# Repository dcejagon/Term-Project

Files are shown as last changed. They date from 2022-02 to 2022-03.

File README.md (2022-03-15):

# Term Project Report 
### Description 
For our term project, have designed a 2.5 axis plotter. This plotter will have 
a rotating arm with a carriage that extends out on the arm. The plotter will move
in both the R and Theta directions to achieve the plotting of an image. 
arm, with the actual pen extending out on the arm. The base of the plotter will 
hold 2 motors; the first motor will control the rotation of the arm similar to 
the motion of  a windshield wiper (Theta), while the second motor will change the radial 
position of the pen carrier(R). The radial motor will control the pen location by 
moving the sharpie carriage using belts driven by pulleys. The pen carriage will have a servo motor 
that controls the up and down motion of the pen (0.5 Axis). This plotter will 
convert an image to X-Y Gcode, and then we will convert that into cylindrical, 
R-Theta, coordinates due to our system being inherently non-rectilinear. 
In addition, This plotter should be relatively low cost ~$15 per person. 
We intend to use materials commonly used in 3D printing like Aluminum T-Slot 
extrusion and V-Slot bearings. The full bill of materials and cost breakdown 
is seen below. Items that have a "-" in the cost column are parts that we have 
access to with no cost. Our main source for parts will be Amazon to eliminate 
shipping costs. Team members have access to 3D printers, which will be used 
to fabricate custom parts such as mounting brackets, main Sharpie carriage, 
and motor mounts at no additional cost.  
### Use
This 2.5 axis plotter is intended to be used to plot images on a piece of paper. 
However, the main carriage of this plotter could be easily changed to accommodate 
a CO2 laser or small cutting blade to turn the plotter into a laser cutter or a 
vinyl cutter.  This project was just intended to be used by our team to demonstrate
many of the concepts that we learned in ME 405, Mechatronics, however I think it would 
be interesting to redesign some of the motor mounts to accept more consumer grade motors
so that we could each produce our own plotter for personal use. 
### BOM and Estimated Cost
| Qty. | Part | Source | Est. Cost |
|:----:|:---|:---|:---:|
|  2 | Pittperson Gearmotors | ME405 Tub | - |
|  1 | Nucleo with Shoe | ME405 Tub | - |
|  1 | Motor H-Bridge | ME405 Tub | - |
|  1 | Purple Sharpie&trade; | Personal Supply | - |
|  1 | Servo Motor | Personal Supply | - |
|  1 | Limit Switch pack | Amazon | $6.99 |
|  1 | Vbearings and Belt | Amazon | $18.59  |
|  1 | 2020 Al Extrusion | Amazon | $19.99  |

### Sketch of Pen Plotter 
The initial sketch of our system is shown below. This design features preliminary
dimensions and a sketch of the general shape and motion of our system. The blue lines
depict the direction that the system may move, and the axis that this motion occurs on.
For example, the curved blue arrows and the Theta axis show that our "arm" will rotate
about the larger base (Radius of 1"). The main features of this sketch are the base,
arm, carriage, and wheel. The exact shape and location of these parts, along with 
parts that are less significant to the general motion of our system are shown in the 
full system CAD model below. One thing that is not depicted in this sketch is how 
we actuated the 0.5 axis that will move the Sharpie up and down. This will be shown
in detail in the Main Carriage Subsystem CAD model section below. 

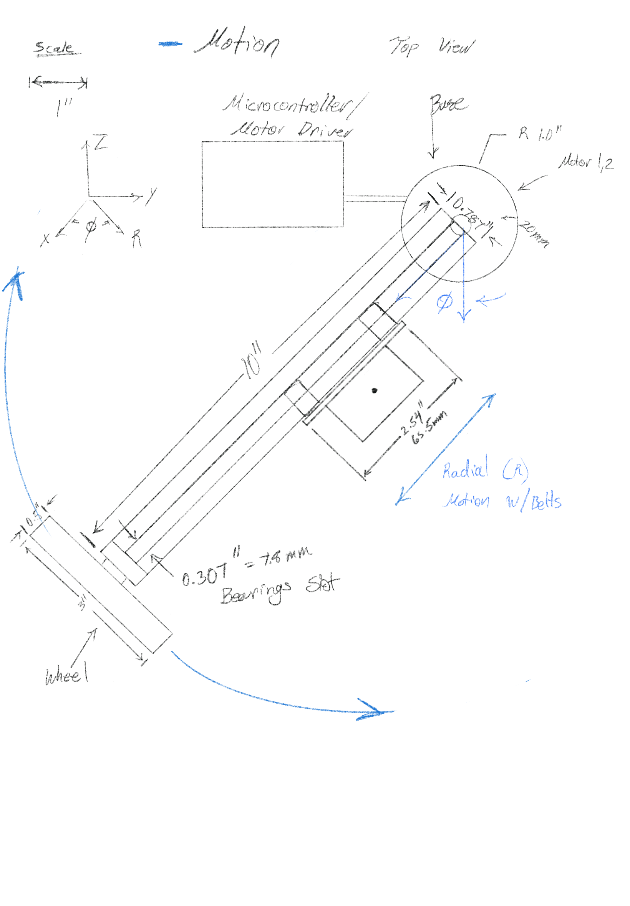
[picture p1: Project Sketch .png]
Drawing of Proposed Plotter

Initial Sketch of Plotter 

### Full System CAD Model
The image below shows our full system CAD model. The parts that are a light orange 
color are some the parts that we 3D printed. This image shows how the system will move;
the motor that is attached to the aluminum extrusion will rotate a pulley. This pulley 
will rotate a belt, who's ends are attached to the sharpie carriage in the slots. The
belt will be tensioned by being attached to a idle pulley on the aluminum extrusion
near the wheel.

The theta direction will also be actuated with belts and pulleys. The Theta motor
is fixed with set screws into the large, orange, triangle shaped, bracket. This motor 
has a pulley on it that is in plane with the larger red pulley in the image. These pulleys
have a belt that is attached around them, so when the motor rotates, the large 
pulley is rotated. This large red pulley is fixed to the aluminum extrusion with 
two bolts. This means that the red pulley cannot rotate relative to the extrusion,
which allows us to rotate the extrusion by rotating the Theta motor. This pulley is 
extended to hold three ball bearings that are press fit into the pulley. 
These bearings rotate on a 3/8" bolt which is the "axle" for our arm to rotate on.
In addition, the red pulley is around twice the diameter of the pulley attached to the motor 
which gives us a larger gear ratio to transmit more torque from the motor to our system. 

The large wheel on the end of the extrusion is necessary to provide support to the 
end of our arm. The wheel prevents the arm from being a cantilevered beam, and reduces
the torque required to rotate the arm. 

Each of the motor mounting brackets have holes that have heat set inserts in them
so we can use screws to act as set screws to hold the motors in place. 

The motor bracket on the aluminum extrusion also holds a limit switch. This switch 
will act as a "kill switch" so that if the motor ever hits it, the motor duty will 
instantly be set to zero. This switch was initially going to be used to home the R
axis, however we had an issue where our motors would free-spin after the program finished
running, and changing the switch to be a kill switch prevents the mechanical system 
from tearing itself apart and the motors from burning up. 

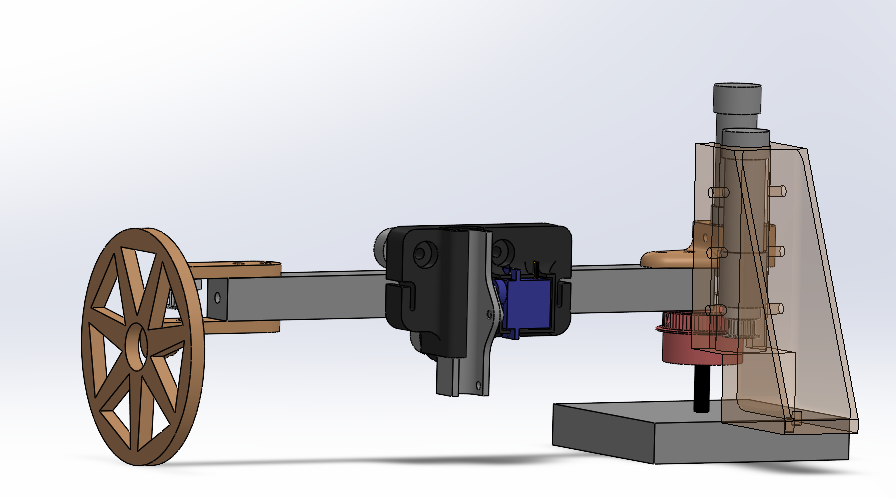
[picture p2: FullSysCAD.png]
CAD of Full System, Front

CAD model of full system front view

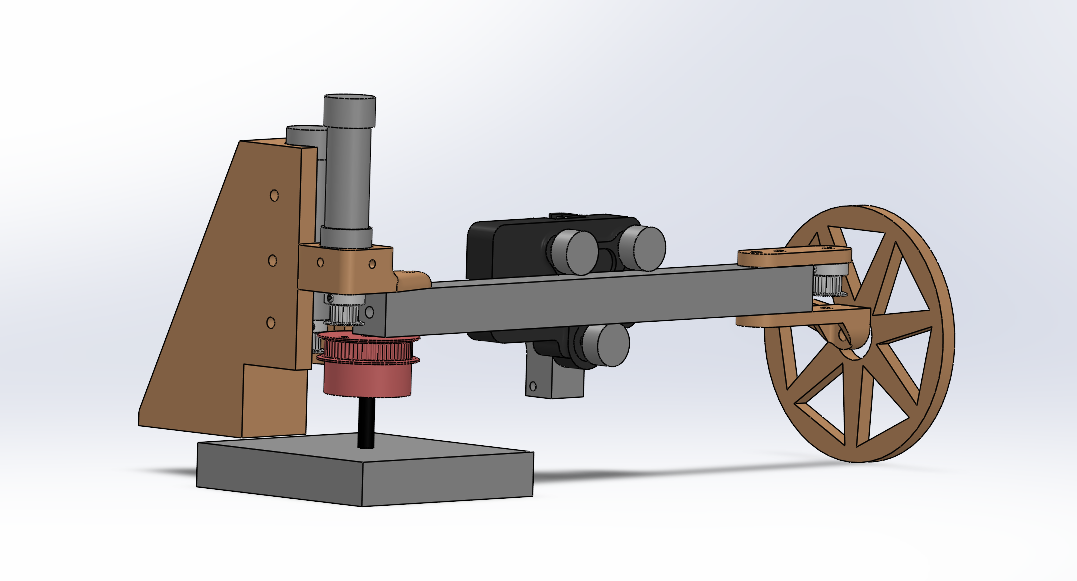
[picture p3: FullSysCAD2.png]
CAD of Full System, Rear

CAD model of full system rear view

### Main Carriage Subsystem CAD Model

The image below shows the main sharpie carriage in more detail. The black piece
is the "carriage" that has bolts that go through it and have V-Slot bearings on
the back side (shown as the gray cylinders at the top of the image). These bearings
ride in the T-slot on the aluminum extrusion, allowing for smooth, linear movement
of the carriage on the extrusion. 

The blue rectangular piece is the servo motor that is responsible for actuating our 
half axis. The servo motor is attached to the carriage with rubber bands so it can
be repurposed for other projects. The servo motor has a small link (white part) attached to it.
This link has a hole on one side to press fit onto the servo shaft, and a slot 
on the other. This slot will have a "pin" that attaches to the sliding carriage 
where the Sharpie is attached. When the servo motor is rotated, the slotted linkage
rotates , which pushes against pin attached to the Sharpie carriage, causing 
vertical movement of the Sharpie carriage. 

The small, "r" shaped slots on either side of the main carriage are where the ends
of the belt to move the main carriage are attached.  

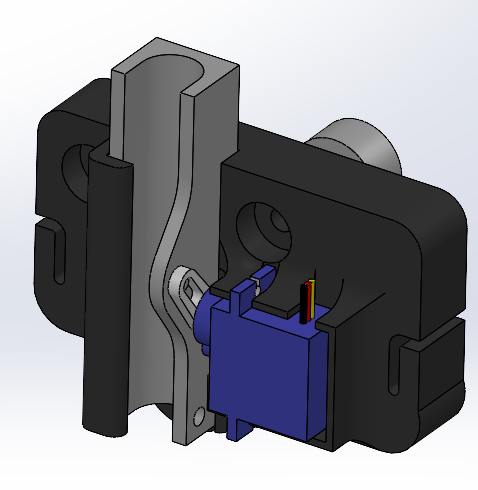
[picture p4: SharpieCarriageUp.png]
CAD of main carriage, raised

CAD model of main carriage in "up" position

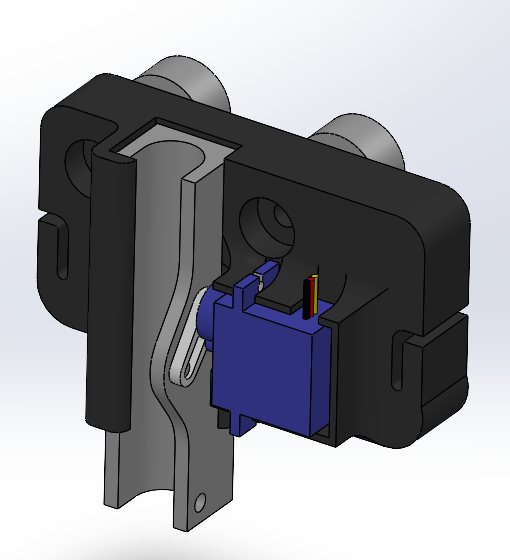
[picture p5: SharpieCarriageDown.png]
CAD of main carriage, lowered

CAD model of main carriage in "down" position

### Software Design Overview
In order to generate the path that the pen should take, we used http://jscut.org/jscut.html# ,
a website that accepts SVG images and converts it to GCODE. This website was nice, because 
each of the GCODE lines were G1, which is the call for a straight line. The GCODE that 
this website outputs is a series of straight lines that are very short (around 0.001"). 
This means, we essentially have a list of X-Y coordinates that trace out our image. 

We then use the file GcodeInterpreter.py, to take each line of GCODE, pull out the 
desired X-Y coordinates, and then preform some math to convert these to R-Theta
coordinates. From these R-Theta coordinates, we use our known gear ratios to write
the desired R Motor angle and Theta Motor angle to their own .txt files. 

We then read each line of these files one at a time, to generate the desired
R and Theta motor setpoints. 

We then input these setpoints into a closed loop controller which will calculate the
required duty to move the motor so that the motor position reaches the setpoint. 

We determine the motor position from encoders that are attached to the motor shaft. 

The timing of these different tasks was something that we had some trouble implementing,
however, we were able to achieve the proper timing by adding two buffer variables. 
Essentially, first, we get both setpoints, then, the motors rotate to try and reach that setpoint
next, we check to see if each motor has reached its setpoint (or within a few degrees of it).
If the motor has not reached this setpoint, we do not get another setpoint. As soon as the motor 
reaches its setpoint, on its next loop around the task diagram, we generate a new setpoint. 
This process allows us to be sure that our motors reach their desired setpoint before they
transition to another one. 

In addition, the motor control task has three sub-tasks running. 
First, we read the motor position from the encoders. Next, we run the closed loop
controller. Last, we use the motor duty that comes out of the closed loop file
to run our motors at this duty. It is important that the motor control task runs 
as quickly as possible so that the closed loop controller can calculate be sure the
motor reaches the desired position as quickly as possible, while minimizing overshoot. 

Lastly, we had a task that controlled the limit switch reading and servo motor actuation.
The limit switch subtask checks the limit switch value (0 or 1) and decides if the duty needs to be set 
to zero. The servo motor subtask checks to see if the pen should lifted or lowered,
and then raised or lowers the servo motor. 

A more in-depth description of each file, along with the overall software structure
can be found in the links below. 

Full Source Code:          [https://github.com/dcejagon/Term-Project/blob/e9a6a358911b557f958eb8ccfb334c0a805cc6d8/src]

Documentation:             [https://dcejagon.github.io/Term-Project/index.html]

### System Performance and Results
We tested our system by trying to draw several images. We attempted to draw a 
Cal Poly logo, as well as a simple rectangle. These test revealed some errors
in our software design somewhere. We were able to successfully draw, however, we
were not able to produce a discernable image. We believe that it has something to 
do with the path the pen is taking between the points. For the rectangle, we can see
the image has four distinct "points", but the paths between these points is anything 
but a straight line. With more time, we would be able to hammer out the bugs in
our system and correct the paths between points. Overall, we are happy with what 
we were able to accomplish during the entirety of this project. 

### Possible System Modifications
Outside of the path issue mentioned above, one of our biggest issues was the 
resolution our motors were able to accomplish. We think that we prioritized speed 
more than accuracy, which means we tried to minimize the gear ratios that we were 
using. The motors we were using have a minimum duty that will make them rotate. 
Significant issues arise when the desired position is too close to the previous 
position, because the motor cannot rotate with this small of a duty. By increasing 
the gear ratios we are using significantly, we would increase the resolution that 
we can plot. Instead of 2 points that are very close producing a duty of 10 for example,
with the increased gear ratio, we can have the same two points, produce a duty of 50 or even 100.
This would allow for our plotted pictures to be very clear, with the effect of 
significantly decreasing the speed at which we can plot. 

In addition, we should have had our platform 
that the parts are mounted to extend out so that every part of the system rests
on this platform. This would minimize the amount of flex from the point of rotation
to the end of the extrusion. 

One of the last things that was somewhat of an issue, was our heat set inserts. 
When we tightened the screws to hold the motor in place, the inserts began to pull 
out of their holes. We think this could be resolved by reducing the size of the holes
or using different inserts. 

Some of the things that do not need modification is how the main carriage rides on
the aluminum extrusion. We are able to produce a very smooth linear movement of the
carriage when we rotate the motor. In addition, the way the way our different tasks
interacted with each other was largely successful. Once we figured out the proper 
timing, our software worked as intended, and ironing out the path issue would
not require much rework to our task layout. 

Here is the link to the folder that contains all of our Solidworks files as well
as STL's used for 3D printing. 
[https://github.com/dcejagon/Term-Project/tree/bce21b94aa009a9af5754362cd7ddc3f18eb79eb/TP%20CAD]

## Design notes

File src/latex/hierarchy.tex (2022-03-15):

\doxysection{Class Hierarchy}
This inheritance list is sorted roughly, but not completely, alphabetically\+:\begin{DoxyCompactList}
\item \contentsline{section}{task\+\_\+share.\+Base\+Share}{\pageref{classtask__share_1_1BaseShare}}{}
\begin{DoxyCompactList}
\item \contentsline{section}{task\+\_\+share.\+Queue}{\pageref{classtask__share_1_1Queue}}{}
\item \contentsline{section}{task\+\_\+share.\+Share}{\pageref{classtask__share_1_1Share}}{}
\end{DoxyCompactList}
\item \contentsline{section}{Encoder\+Driver.\+Encoder\+Driver}{\pageref{classEncoderDriver_1_1EncoderDriver}}{}
\item \contentsline{section}{REncoder.\+Encoder\+Driver}{\pageref{classREncoder_1_1EncoderDriver}}{}
\item \contentsline{section}{Gcode\+Interpreter.\+Gcode\+Interpreter}{\pageref{classGcodeInterpreter_1_1GcodeInterpreter}}{}
\item \contentsline{section}{Servo\+Motor\+F.\+Limit\+Switch}{\pageref{classServoMotorF_1_1LimitSwitch}}{}
\item \contentsline{section}{Motor\+Driver.\+Motor\+Driver}{\pageref{classMotorDriver_1_1MotorDriver}}{}
\item \contentsline{section}{shares.\+Queue}{\pageref{classshares_1_1Queue}}{}
\item \contentsline{section}{RMotor\+Control.\+RClosed\+Loop}{\pageref{classRMotorControl_1_1RClosedLoop}}{}
\item \contentsline{section}{Servo\+Motor\+F.\+Servo\+MotorF}{\pageref{classServoMotorF_1_1ServoMotorF}}{}
\item \contentsline{section}{shares.\+Share}{\pageref{classshares_1_1Share}}{}
\item \contentsline{section}{cotask.\+Task}{\pageref{classcotask_1_1Task}}{}
\item \contentsline{section}{cotask.\+Task\+List}{\pageref{classcotask_1_1TaskList}}{}
\item \contentsline{section}{Theta\+Motor\+Control.\+Theta\+Closed\+Loop}{\pageref{classThetaMotorControl_1_1ThetaClosedLoop}}{}
\end{DoxyCompactList}

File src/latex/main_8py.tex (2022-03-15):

\hypertarget{main_8py}{}\doxysection{main.\+py File Reference}
\label{main_8py}\index{main.py@{main.py}}

File to control the main function of our hardware.  

\doxysubsection*{Functions}
\begin{DoxyCompactItemize}
\item 
\mbox{\Hypertarget{main_8py_a4b8585ab93623990a26b69bcdc14b238}\label{main_8py_a4b8585ab93623990a26b69bcdc14b238}} 
def {\bfseries main.\+task1\+\_\+fun} ()
\begin{DoxyCompactList}\small\item\em ! runs tasks and functions for the first motor \end{DoxyCompactList}\item 
\mbox{\Hypertarget{main_8py_a6a1e59f7b9547c8b4149f09992218273}\label{main_8py_a6a1e59f7b9547c8b4149f09992218273}} 
def {\bfseries main.\+task2\+\_\+fun} ()
\item 
\mbox{\Hypertarget{main_8py_acc62ac11d1a297e1641a94216ce982c7}\label{main_8py_acc62ac11d1a297e1641a94216ce982c7}} 
def {\bfseries main.\+task3\+\_\+fun} ()
\end{DoxyCompactItemize}
\doxysubsection*{Variables}
\begin{DoxyCompactItemize}
\item 
\mbox{\hyperlink{main_8py_a87970a5d04059649a6735a2a405477ea}{main.\+en\+\_\+pin}} = pyb.\+Pin (pyb.\+Pin.\+board.\+PA10, pyb.\+Pin.\+OUT\+\_\+\+PP)
\begin{DoxyCompactList}\small\item\em This variable is for the enable pin for motor 1. \end{DoxyCompactList}\item 
\mbox{\hyperlink{main_8py_aad671708cd06aec861a24b45c56c74aa}{main.\+in1pin}} = pyb.\+Pin (pyb.\+Pin.\+board.\+PB4, pyb.\+Pin.\+OUT\+\_\+\+PP)
\begin{DoxyCompactList}\small\item\em This variable is for the first pin of motor 1. \end{DoxyCompactList}\item 
\mbox{\hyperlink{main_8py_ae821c4ba5f2d29414e6008d3caaf5109}{main.\+in2pin}} = pyb.\+Pin (pyb.\+Pin.\+board.\+PB5, pyb.\+Pin.\+OUT\+\_\+\+PP)
\begin{DoxyCompactList}\small\item\em This variable is for the second pin of motor 1. \end{DoxyCompactList}\item 
\mbox{\Hypertarget{main_8py_a4fe20a9d36fdc5b4ea50d88f43f6ed54}\label{main_8py_a4fe20a9d36fdc5b4ea50d88f43f6ed54}} 
int {\bfseries main.\+timer} = 3
\begin{DoxyCompactList}\small\item\em This variable is for the timer number associated with motor 1. \end{DoxyCompactList}\item 
\mbox{\hyperlink{main_8py_aa7d20efaf3b8775924472f1e6ee9abe1}{main.\+en\+\_\+pin2}} = pyb.\+Pin (pyb.\+Pin.\+board.\+PC1, pyb.\+Pin.\+OUT\+\_\+\+PP)
\begin{DoxyCompactList}\small\item\em This variable is for the enable pin for motor 2. \end{DoxyCompactList}\item 
\mbox{\hyperlink{main_8py_af69bac68438b6a4b323fd2da4fb0ab10}{main.\+in1pin2}} = pyb.\+Pin (pyb.\+Pin.\+board.\+PA0, pyb.\+Pin.\+OUT\+\_\+\+PP)
\begin{DoxyCompactList}\small\item\em This variable is for the first pin of motor 2. \end{DoxyCompactList}\item 
\mbox{\hyperlink{main_8py_ae006dd22d15c7224f4271cdd30be3c3e}{main.\+in2pin2}} = pyb.\+Pin (pyb.\+Pin.\+board.\+PA1, pyb.\+Pin.\+OUT\+\_\+\+PP)
\begin{DoxyCompactList}\small\item\em This variable is for the second pin of motor 2. \end{DoxyCompactList}\item 
\mbox{\Hypertarget{main_8py_ab6598c969df592e6fefba95d3ae53da0}\label{main_8py_ab6598c969df592e6fefba95d3ae53da0}} 
int {\bfseries main.\+timer2} = 5
\begin{DoxyCompactList}\small\item\em This variable is for the timer number associated with motor 2. \end{DoxyCompactList}\item 
\mbox{\hyperlink{main_8py_a9302e8220a79b02f30da6df3b3b72db9}{main.\+ENCpin1}} = pyb.\+Pin (pyb.\+Pin.\+board.\+PB6)
\begin{DoxyCompactList}\small\item\em This variable is for the frist encoder pin of encoder 1. \end{DoxyCompactList}\item 
\mbox{\hyperlink{main_8py_a335a37a6d6e27c40302538c0b03bea08}{main.\+ENCpin2}} = pyb.\+Pin (pyb.\+Pin.\+board.\+PB7)
\begin{DoxyCompactList}\small\item\em This variable is for the second encoder pin of encoder 1. \end{DoxyCompactList}\item 
\mbox{\Hypertarget{main_8py_aee15e1a13ec15c40e22322b1ca997d5a}\label{main_8py_aee15e1a13ec15c40e22322b1ca997d5a}} 
int {\bfseries main.\+timernumber} = 4
\begin{DoxyCompactList}\small\item\em This variable is for the timer number associated with encoder 1. \end{DoxyCompactList}\item 
\mbox{\hyperlink{main_8py_a630b3ace839f6b7b34761f44d2161d6e}{main.\+ENC2pin1}} = pyb.\+Pin (pyb.\+Pin.\+board.\+PC6)
\begin{DoxyCompactList}\small\item\em This variable is for the frist encoder pin of encoder 2. \end{DoxyCompactList}\item 
\mbox{\hyperlink{main_8py_a4c4b6becca7ef9e44742e3eecca211a9}{main.\+ENC2pin2}} = pyb.\+Pin (pyb.\+Pin.\+board.\+PC7)
\begin{DoxyCompactList}\small\item\em This variable is for the second encoder pin of encoder 2. \end{DoxyCompactList}\item 
\mbox{\Hypertarget{main_8py_ac52fc1272d4326318676d53ec92ad746}\label{main_8py_ac52fc1272d4326318676d53ec92ad746}} 
int {\bfseries main.\+timernumber2} = 8
\begin{DoxyCompactList}\small\item\em This variable is for the timer number associated with encoder 2. \end{DoxyCompactList}\item 
\mbox{\hyperlink{main_8py_a4f911a1828df7baf0a3e060305223057}{main.\+duty1}} = \mbox{\hyperlink{classtask__share_1_1Share}{task\+\_\+share.\+Share}} (\textquotesingle{}f\textquotesingle{}, thread\+\_\+protect = False, name = \char`\"{}Duty\+\_\+1\char`\"{})
\begin{DoxyCompactList}\small\item\em Shared Variable for duty of motor 1. \end{DoxyCompactList}\item 
\mbox{\hyperlink{main_8py_ac52b4d68543efdb75c86ea26b8171085}{main.\+duty2}} = \mbox{\hyperlink{classtask__share_1_1Share}{task\+\_\+share.\+Share}} (\textquotesingle{}f\textquotesingle{}, thread\+\_\+protect = False, name = \char`\"{}Duty\+\_\+2\char`\"{})
\begin{DoxyCompactList}\small\item\em Shared Variable for duty of motor 2. \end{DoxyCompactList}\item 
\mbox{\hyperlink{main_8py_a35d82fc6f6309ca098efc4fb6ab555ff}{main.\+Enc\+Position}} = \mbox{\hyperlink{classtask__share_1_1Share}{task\+\_\+share.\+Share}} (\textquotesingle{}h\textquotesingle{}, thread\+\_\+protect = False, name = \char`\"{}Position\+\_\+1\char`\"{})
\begin{DoxyCompactList}\small\item\em Shared Variable position of encoder 1. \end{DoxyCompactList}\item 
\mbox{\hyperlink{main_8py_a9ba3c81db34dbcdf4b55584e0f0fb2e2}{main.\+Enc\+Position2}} = \mbox{\hyperlink{classtask__share_1_1Share}{task\+\_\+share.\+Share}} (\textquotesingle{}h\textquotesingle{}, thread\+\_\+protect = False, name = \char`\"{}Position\+\_\+2\char`\"{})
\begin{DoxyCompactList}\small\item\em Shared Variable position of encoder 2. \end{DoxyCompactList}\item 
\mbox{\hyperlink{main_8py_a1a9d6b768cfb91f02bd7d18cdc9fbd20}{main.\+Kp1}} = \mbox{\hyperlink{classtask__share_1_1Share}{task\+\_\+share.\+Share}} (\textquotesingle{}f\textquotesingle{}, thread\+\_\+protect = False, name = \char`\"{}Proportional\+\_\+\+Gain1\char`\"{})
\begin{DoxyCompactList}\small\item\em Shared variable for proportional gain of motor 1. \end{DoxyCompactList}\item 
\mbox{\hyperlink{main_8py_ab96cfd6fecea16d8801129f649f7b971}{main.\+Kp2}} = \mbox{\hyperlink{classtask__share_1_1Share}{task\+\_\+share.\+Share}} (\textquotesingle{}f\textquotesingle{}, thread\+\_\+protect = False, name = \char`\"{}Proportional\+\_\+\+Gain2\char`\"{})
\begin{DoxyCompactList}\small\item\em Shared variable for proportional gain of motor 2. \end{DoxyCompactList}\item 
\mbox{\hyperlink{main_8py_a7b85b2b65758a558f3e3032f3950c355}{main.\+setpoint1}} = \mbox{\hyperlink{classtask__share_1_1Share}{task\+\_\+share.\+Share}} (\textquotesingle{}f\textquotesingle{}, thread\+\_\+protect = False, name = \char`\"{}Set\+\_\+\+Point1\char`\"{})
\begin{DoxyCompactList}\small\item\em Shared variable for the setpoint of motor 1. \end{DoxyCompactList}\item 
\mbox{\hyperlink{main_8py_aaa37d4ce2366d78815bdf5dd79d8cc08}{main.\+setpoint2}} = \mbox{\hyperlink{classtask__share_1_1Share}{task\+\_\+share.\+Share}} (\textquotesingle{}f\textquotesingle{}, thread\+\_\+protect = False, name = \char`\"{}Set\+\_\+\+Point2\char`\"{})
\begin{DoxyCompactList}\small\item\em Shared variable for the setpoint of motor 2. \end{DoxyCompactList}\item 
\mbox{\hyperlink{main_8py_ac3ee7e26a582192f6abba62394fd964d}{main.\+zpos}} = \mbox{\hyperlink{classtask__share_1_1Share}{task\+\_\+share.\+Share}} (\textquotesingle{}h\textquotesingle{}, thread\+\_\+protect = False, name = \char`\"{}z\+\_\+\+Position\char`\"{})
\begin{DoxyCompactList}\small\item\em Shared variable for the z position for our half axis. \end{DoxyCompactList}\item 
\mbox{\hyperlink{main_8py_a8c2153a050d8d0173f8bb43ef99e7174}{main.\+THETAGO}} = \mbox{\hyperlink{classtask__share_1_1Share}{task\+\_\+share.\+Share}} (\textquotesingle{}h\textquotesingle{}, thread\+\_\+protect = False, name = \char`\"{}THETAGO\char`\"{})
\begin{DoxyCompactList}\small\item\em Shared variable to tell us when theta is ready to move. \end{DoxyCompactList}\item 
\mbox{\hyperlink{main_8py_abd2743711754e3648f956f6c3889ab8d}{main.\+RGO}} = \mbox{\hyperlink{classtask__share_1_1Share}{task\+\_\+share.\+Share}} (\textquotesingle{}h\textquotesingle{}, thread\+\_\+protect = False, name = \char`\"{}RGO\char`\"{})
\begin{DoxyCompactList}\small\item\em Shared variable to tell us when R is ready to move. \end{DoxyCompactList}\item 
\mbox{\hyperlink{main_8py_a2710766abdf6f3767409cc7642c71148}{main.\+Rswitch}} = \mbox{\hyperlink{classtask__share_1_1Share}{task\+\_\+share.\+Share}} (\textquotesingle{}h\textquotesingle{}, thread\+\_\+protect = False, name = \char`\"{}R\+\_\+\+Switch\char`\"{})
\begin{DoxyCompactList}\small\item\em Shared variable for the value of our R limit switch. \end{DoxyCompactList}\item 
\mbox{\Hypertarget{main_8py_a3a2f088acede9b226beb08b70c42f146}\label{main_8py_a3a2f088acede9b226beb08b70c42f146}} 
{\bfseries main.\+motor1} = \mbox{\hyperlink{classMotorDriver_1_1MotorDriver}{Motor\+Driver.\+Motor\+Driver}}(en\+\_\+pin, en\+\_\+pin2, in1pin, in2pin, in1pin2, in2pin2, timer, timer2,duty1,duty2)
\begin{DoxyCompactList}\small\item\em Variable for the Motor 1 object. \end{DoxyCompactList}\item 
\mbox{\Hypertarget{main_8py_a1a2262732e6726079ffed3e075851a70}\label{main_8py_a1a2262732e6726079ffed3e075851a70}} 
{\bfseries main.\+motor2} = \mbox{\hyperlink{classMotorDriver_1_1MotorDriver}{Motor\+Driver.\+Motor\+Driver}}(en\+\_\+pin, en\+\_\+pin2, in1pin, in2pin, in1pin2, in2pin2, timer, timer2,duty1,duty2)
\begin{DoxyCompactList}\small\item\em Variable for the Motor 2 object. \end{DoxyCompactList}\item 
\mbox{\Hypertarget{main_8py_aab5c7095975a4a61d864fc7509ca8bbf}\label{main_8py_aab5c7095975a4a61d864fc7509ca8bbf}} 
{\bfseries main.\+ENC1} = \mbox{\hyperlink{classEncoderDriver_1_1EncoderDriver}{Encoder\+Driver.\+Encoder\+Driver}}(ENCpin1,ENCpin2,ENC2pin1,ENC2pin2,timernumber,timernumber2,Enc\+Position,Enc\+Position2)
\begin{DoxyCompactList}\small\item\em Variable for the Encoder 1 object. \end{DoxyCompactList}\item 
\mbox{\Hypertarget{main_8py_a1210f3cb932d9e73c75066d4d6bdf458}\label{main_8py_a1210f3cb932d9e73c75066d4d6bdf458}} 
{\bfseries main.\+ENC2} = \mbox{\hyperlink{classREncoder_1_1EncoderDriver}{REncoder.\+Encoder\+Driver}}(ENC2pin1,ENC2pin2,timernumber2,Enc\+Position2)
\begin{DoxyCompactList}\small\item\em Variable for the Encoder 2 object. \end{DoxyCompactList}\item 
\mbox{\Hypertarget{main_8py_a7e9c0d166ccbb8661b586c8263f78a30}\label{main_8py_a7e9c0d166ccbb8661b586c8263f78a30}} 
{\bfseries main.\+Theta\+Control} = \mbox{\hyperlink{classThetaMotorControl_1_1ThetaClosedLoop}{Theta\+Motor\+Control.\+Theta\+Closed\+Loop}}(Kp1,setpoint1,Enc\+Position,duty1,THETAGO)
\begin{DoxyCompactList}\small\item\em Variable for the Theta Control Loop object. \end{DoxyCompactList}\item 
\mbox{\Hypertarget{main_8py_a874c858cb654417e02a4f0db017e74e7}\label{main_8py_a874c858cb654417e02a4f0db017e74e7}} 
{\bfseries main.\+RControl} = \mbox{\hyperlink{classRMotorControl_1_1RClosedLoop}{RMotor\+Control.\+RClosed\+Loop}}(Kp2,setpoint2,Enc\+Position2,duty2,RGO)
\begin{DoxyCompactList}\small\item\em Variable for the R Control Loop object. \end{DoxyCompactList}\item 
\mbox{\hyperlink{main_8py_a0f8b18d269c2a71d1bedf53f2ce94c12}{main.\+servopin}} = pyb.\+Pin (pyb.\+Pin.\+board.\+PA7, pyb.\+Pin.\+OUT\+\_\+\+PP)
\begin{DoxyCompactList}\small\item\em Variable for the pin our servo motor is connected to. \end{DoxyCompactList}\item 
\mbox{\Hypertarget{main_8py_a461a2c2db2e55486d5bdf200e0493f04}\label{main_8py_a461a2c2db2e55486d5bdf200e0493f04}} 
int {\bfseries main.\+servotimer} = 17
\begin{DoxyCompactList}\small\item\em Variable for the timer for our servo motor pin (timer 17) \end{DoxyCompactList}\item 
\mbox{\Hypertarget{main_8py_a4c160551babfe5fa0fa89486d6af4595}\label{main_8py_a4c160551babfe5fa0fa89486d6af4595}} 
int {\bfseries main.\+servoch} = 1
\begin{DoxyCompactList}\small\item\em Variable for the timer for our servo motor cahnnel (ch 1) \end{DoxyCompactList}\item 
\mbox{\hyperlink{main_8py_addd6eb1e79cd691ae9c336b0851e355f}{main.\+switchpin1}} = pyb.\+Pin(pyb.\+Pin.\+board.\+PA8, pyb.\+Pin.\+IN, pyb.\+Pin.\+PULL\+\_\+\+DOWN)
\begin{DoxyCompactList}\small\item\em Variable for the pin our first limit switch is connected to. \end{DoxyCompactList}\item 
\mbox{\hyperlink{main_8py_abde9446db54730de9ad440618259af91}{main.\+switchpin2}} = pyb.\+Pin(pyb.\+Pin.\+board.\+PA6, pyb.\+Pin.\+IN, pyb.\+Pin.\+PULL\+\_\+\+DOWN)
\begin{DoxyCompactList}\small\item\em Variable for the pin our second limit switch is connected to. \end{DoxyCompactList}\item 
\mbox{\Hypertarget{main_8py_a0456f0f43e096d567ddea18f22344039}\label{main_8py_a0456f0f43e096d567ddea18f22344039}} 
{\bfseries main.\+Servo} = \mbox{\hyperlink{classServoMotorF_1_1ServoMotorF}{Servo\+Motor\+F.\+Servo\+MotorF}}(servopin, servotimer, servoch)
\begin{DoxyCompactList}\small\item\em Variable for the servo motor object. \end{DoxyCompactList}\item 
\mbox{\Hypertarget{main_8py_a46ad352c354399c37599ce03c5b47b15}\label{main_8py_a46ad352c354399c37599ce03c5b47b15}} 
{\bfseries main.\+LSwitch} = \mbox{\hyperlink{classServoMotorF_1_1LimitSwitch}{Servo\+Motor\+F.\+Limit\+Switch}}(switchpin1,switchpin2,duty2,Rswitch)
\begin{DoxyCompactList}\small\item\em Variable for the limit switch object. \end{DoxyCompactList}\item 
\mbox{\Hypertarget{main_8py_a8d216d76ebd2f897ab8010e2890ee21e}\label{main_8py_a8d216d76ebd2f897ab8010e2890ee21e}} 
{\bfseries main.\+x} = int(input())
\item 
\mbox{\hyperlink{main_8py_af4b8f4290f8d32e70654f6deb864787f}{main.\+task1}}
\item 
\mbox{\hyperlink{main_8py_a99d189b8f9eb3784cf7d4e5c3241b562}{main.\+task2}}
\item 
\mbox{\hyperlink{main_8py_a120516a5d42c212c898d4616d266077a}{main.\+task3}}
\item 
\mbox{\Hypertarget{main_8py_a5854bd125b139389df502649ad7b0c9c}\label{main_8py_a5854bd125b139389df502649ad7b0c9c}} 
{\bfseries main.\+vcp} = pyb.\+USB\+\_\+\+VCP ()
\end{DoxyCompactItemize}

\doxysubsection{Detailed Description}
File to control the main function of our hardware. 

\begin{DoxyAuthor}{Author}
Daniel Gonzalez 

Nolan Clapp 

Caleb Kephart 
\end{DoxyAuthor}
\begin{DoxyDate}{Date}
February 7, 2022 
\end{DoxyDate}

\doxysubsection{Variable Documentation}
\mbox{\Hypertarget{main_8py_a4f911a1828df7baf0a3e060305223057}\label{main_8py_a4f911a1828df7baf0a3e060305223057}} 
\index{main.py@{main.py}!duty1@{duty1}}
\index{duty1@{duty1}!main.py@{main.py}}
\doxysubsubsection{\texorpdfstring{duty1}{duty1}}
{\footnotesize\ttfamily main.\+duty1 = \mbox{\hyperlink{classtask__share_1_1Share}{task\+\_\+share.\+Share}} (\textquotesingle{}f\textquotesingle{}, thread\+\_\+protect = False, name = \char`\"{}Duty\+\_\+1\char`\"{})}

Shared Variable for duty of motor 1. 

This shared variable for the duty of motor 1 is set up to be a float. This is important because when we write to this variable in our closed loop controller, the number we calculate is a float. \mbox{\Hypertarget{main_8py_ac52b4d68543efdb75c86ea26b8171085}\label{main_8py_ac52b4d68543efdb75c86ea26b8171085}} 
\index{main.py@{main.py}!duty2@{duty2}}
\index{duty2@{duty2}!main.py@{main.py}}
\doxysubsubsection{\texorpdfstring{duty2}{duty2}}
{\footnotesize\ttfamily main.\+duty2 = \mbox{\hyperlink{classtask__share_1_1Share}{task\+\_\+share.\+Share}} (\textquotesingle{}f\textquotesingle{}, thread\+\_\+protect = False, name = \char`\"{}Duty\+\_\+2\char`\"{})}

Shared Variable for duty of motor 2. 

This shared variable for the duty of motor 2 is set up to be a float. This is important because when we write to this variable in our closed loop controller, the number we calculate is a float. \mbox{\Hypertarget{main_8py_a87970a5d04059649a6735a2a405477ea}\label{main_8py_a87970a5d04059649a6735a2a405477ea}} 
\index{main.py@{main.py}!en\_pin@{en\_pin}}
\index{en\_pin@{en\_pin}!main.py@{main.py}}
\doxysubsubsection{\texorpdfstring{en\_pin}{en\_pin}}
{\footnotesize\ttfamily main.\+en\+\_\+pin = pyb.\+Pin (pyb.\+Pin.\+board.\+PA10, pyb.\+Pin.\+OUT\+\_\+\+PP)}

This variable is for the enable pin for motor 1. 

This variable is responsible for holding the pin information for the pin that will enable motor 1 when it is set to high. The pin is Pin A10. \mbox{\Hypertarget{main_8py_aa7d20efaf3b8775924472f1e6ee9abe1}\label{main_8py_aa7d20efaf3b8775924472f1e6ee9abe1}} 
\index{main.py@{main.py}!en\_pin2@{en\_pin2}}
\index{en\_pin2@{en\_pin2}!main.py@{main.py}}
\doxysubsubsection{\texorpdfstring{en\_pin2}{en\_pin2}}
{\footnotesize\ttfamily main.\+en\+\_\+pin2 = pyb.\+Pin (pyb.\+Pin.\+board.\+PC1, pyb.\+Pin.\+OUT\+\_\+\+PP)}

This variable is for the enable pin for motor 2. 

This variable is responsible for holding the pin information for the pin that will enable motor 2 when it is set to high. The pin is Pin C1. \mbox{\Hypertarget{main_8py_a630b3ace839f6b7b34761f44d2161d6e}\label{main_8py_a630b3ace839f6b7b34761f44d2161d6e}} 
\index{main.py@{main.py}!ENC2pin1@{ENC2pin1}}
\index{ENC2pin1@{ENC2pin1}!main.py@{main.py}}
\doxysubsubsection{\texorpdfstring{ENC2pin1}{ENC2pin1}}
{\footnotesize\ttfamily main.\+ENC2pin1 = pyb.\+Pin (pyb.\+Pin.\+board.\+PC6)}

This variable is for the frist encoder pin of encoder 2. 

This variable sets up the first pin of encoder 2 as Pin BC6 \mbox{\Hypertarget{main_8py_a4c4b6becca7ef9e44742e3eecca211a9}\label{main_8py_a4c4b6becca7ef9e44742e3eecca211a9}} 
\index{main.py@{main.py}!ENC2pin2@{ENC2pin2}}
\index{ENC2pin2@{ENC2pin2}!main.py@{main.py}}
\doxysubsubsection{\texorpdfstring{ENC2pin2}{ENC2pin2}}
{\footnotesize\ttfamily main.\+ENC2pin2 = pyb.\+Pin (pyb.\+Pin.\+board.\+PC7)}

This variable is for the second encoder pin of encoder 2. 

This variable sets up the second pin of encoder 2 as Pin BC7 \mbox{\Hypertarget{main_8py_a9302e8220a79b02f30da6df3b3b72db9}\label{main_8py_a9302e8220a79b02f30da6df3b3b72db9}} 
\index{main.py@{main.py}!ENCpin1@{ENCpin1}}
\index{ENCpin1@{ENCpin1}!main.py@{main.py}}
\doxysubsubsection{\texorpdfstring{ENCpin1}{ENCpin1}}
{\footnotesize\ttfamily main.\+ENCpin1 = pyb.\+Pin (pyb.\+Pin.\+board.\+PB6)}

This variable is for the frist encoder pin of encoder 1. 

This variable sets up the first pin of encoder 1 as Pin B6 \mbox{\Hypertarget{main_8py_a335a37a6d6e27c40302538c0b03bea08}\label{main_8py_a335a37a6d6e27c40302538c0b03bea08}} 
\index{main.py@{main.py}!ENCpin2@{ENCpin2}}
\index{ENCpin2@{ENCpin2}!main.py@{main.py}}
\doxysubsubsection{\texorpdfstring{ENCpin2}{ENCpin2}}
{\footnotesize\ttfamily main.\+ENCpin2 = pyb.\+Pin (pyb.\+Pin.\+board.\+PB7)}

This variable is for the second encoder pin of encoder 1. 

This variable sets up the second pin of encoder 1 as Pin B7 \mbox{\Hypertarget{main_8py_a35d82fc6f6309ca098efc4fb6ab555ff}\label{main_8py_a35d82fc6f6309ca098efc4fb6ab555ff}} 
\index{main.py@{main.py}!EncPosition@{EncPosition}}
\index{EncPosition@{EncPosition}!main.py@{main.py}}
\doxysubsubsection{\texorpdfstring{EncPosition}{EncPosition}}
{\footnotesize\ttfamily main.\+Enc\+Position = \mbox{\hyperlink{classtask__share_1_1Share}{task\+\_\+share.\+Share}} (\textquotesingle{}h\textquotesingle{}, thread\+\_\+protect = False, name = \char`\"{}Position\+\_\+1\char`\"{})}

Shared Variable position of encoder 1. 

This shared variable for the position of motor 1 is set up to be a 16-\/bit unsigned int. This is important because when we write to this variable in our encoder driver, it is a 16 bit number (between 0 and 65535) \mbox{\Hypertarget{main_8py_a9ba3c81db34dbcdf4b55584e0f0fb2e2}\label{main_8py_a9ba3c81db34dbcdf4b55584e0f0fb2e2}} 
\index{main.py@{main.py}!EncPosition2@{EncPosition2}}
\index{EncPosition2@{EncPosition2}!main.py@{main.py}}
\doxysubsubsection{\texorpdfstring{EncPosition2}{EncPosition2}}
{\footnotesize\ttfamily main.\+Enc\+Position2 = \mbox{\hyperlink{classtask__share_1_1Share}{task\+\_\+share.\+Share}} (\textquotesingle{}h\textquotesingle{}, thread\+\_\+protect = False, name = \char`\"{}Position\+\_\+2\char`\"{})}

Shared Variable position of encoder 2. 

This shared variable for the position of motor 2 is set up to be a 16-\/bit unsigned int. This is important because when we write to this variable in our encoder driver, it is a 16 bit number (between 0 and 65535) \mbox{\Hypertarget{main_8py_aad671708cd06aec861a24b45c56c74aa}\label{main_8py_aad671708cd06aec861a24b45c56c74aa}} 
\index{main.py@{main.py}!in1pin@{in1pin}}
\index{in1pin@{in1pin}!main.py@{main.py}}
\doxysubsubsection{\texorpdfstring{in1pin}{in1pin}}
{\footnotesize\ttfamily main.\+in1pin = pyb.\+Pin (pyb.\+Pin.\+board.\+PB4, pyb.\+Pin.\+OUT\+\_\+\+PP)}

This variable is for the first pin of motor 1. 

This variable is set to Pin B4, the first pin on the Neucleo for motor 1. This pin is set as an output. \mbox{\Hypertarget{main_8py_af69bac68438b6a4b323fd2da4fb0ab10}\label{main_8py_af69bac68438b6a4b323fd2da4fb0ab10}} 
\index{main.py@{main.py}!in1pin2@{in1pin2}}
\index{in1pin2@{in1pin2}!main.py@{main.py}}
\doxysubsubsection{\texorpdfstring{in1pin2}{in1pin2}}
{\footnotesize\ttfamily main.\+in1pin2 = pyb.\+Pin (pyb.\+Pin.\+board.\+PA0, pyb.\+Pin.\+OUT\+\_\+\+PP)}

This variable is for the first pin of motor 2. 

This variable is set to Pin A0, the first pin on the Neucleo for motor 2. This pin is set as an output. \mbox{\Hypertarget{main_8py_ae821c4ba5f2d29414e6008d3caaf5109}\label{main_8py_ae821c4ba5f2d29414e6008d3caaf5109}} 
\index{main.py@{main.py}!in2pin@{in2pin}}
\index{in2pin@{in2pin}!main.py@{main.py}}
\doxysubsubsection{\texorpdfstring{in2pin}{in2pin}}
{\footnotesize\ttfamily main.\+in2pin = pyb.\+Pin (pyb.\+Pin.\+board.\+PB5, pyb.\+Pin.\+OUT\+\_\+\+PP)}

This variable is for the second pin of motor 1. 

This variable is set to Pin B5, the first pin on the Neucleo for motor 1. This pin is set as an output. \mbox{\Hypertarget{main_8py_ae006dd22d15c7224f4271cdd30be3c3e}\label{main_8py_ae006dd22d15c7224f4271cdd30be3c3e}} 
\index{main.py@{main.py}!in2pin2@{in2pin2}}
\index{in2pin2@{in2pin2}!main.py@{main.py}}
\doxysubsubsection{\texorpdfstring{in2pin2}{in2pin2}}
{\footnotesize\ttfamily main.\+in2pin2 = pyb.\+Pin (pyb.\+Pin.\+board.\+PA1, pyb.\+Pin.\+OUT\+\_\+\+PP)}

This variable is for the second pin of motor 2. 

This variable is set to Pin A1, the first pin on the Neucleo for motor 2. This pin is set as an output. \mbox{\Hypertarget{main_8py_a1a9d6b768cfb91f02bd7d18cdc9fbd20}\label{main_8py_a1a9d6b768cfb91f02bd7d18cdc9fbd20}} 
\index{main.py@{main.py}!Kp1@{Kp1}}
\index{Kp1@{Kp1}!main.py@{main.py}}
\doxysubsubsection{\texorpdfstring{Kp1}{Kp1}}
{\footnotesize\ttfamily main.\+Kp1 = \mbox{\hyperlink{classtask__share_1_1Share}{task\+\_\+share.\+Share}} (\textquotesingle{}f\textquotesingle{}, thread\+\_\+protect = False, name = \char`\"{}Proportional\+\_\+\+Gain1\char`\"{})}

Shared variable for proportional gain of motor 1. 

This variable is set up as a float so that we can input decimal gains to properly tune our system. This variable is shared between files but is set in the main file. \mbox{\Hypertarget{main_8py_ab96cfd6fecea16d8801129f649f7b971}\label{main_8py_ab96cfd6fecea16d8801129f649f7b971}} 
\index{main.py@{main.py}!Kp2@{Kp2}}
\index{Kp2@{Kp2}!main.py@{main.py}}
\doxysubsubsection{\texorpdfstring{Kp2}{Kp2}}
{\footnotesize\ttfamily main.\+Kp2 = \mbox{\hyperlink{classtask__share_1_1Share}{task\+\_\+share.\+Share}} (\textquotesingle{}f\textquotesingle{}, thread\+\_\+protect = False, name = \char`\"{}Proportional\+\_\+\+Gain2\char`\"{})}

Shared variable for proportional gain of motor 2. 

This variable is set up as a float so that we can input decimal gains to properly tune our system. This variable is shared between files but is set in the main file. \mbox{\Hypertarget{main_8py_abd2743711754e3648f956f6c3889ab8d}\label{main_8py_abd2743711754e3648f956f6c3889ab8d}} 
\index{main.py@{main.py}!RGO@{RGO}}
\index{RGO@{RGO}!main.py@{main.py}}
\doxysubsubsection{\texorpdfstring{RGO}{RGO}}
{\footnotesize\ttfamily main.\+RGO = \mbox{\hyperlink{classtask__share_1_1Share}{task\+\_\+share.\+Share}} (\textquotesingle{}h\textquotesingle{}, thread\+\_\+protect = False, name = \char`\"{}RGO\char`\"{})}

Shared variable to tell us when R is ready to move. 

This variable is calculated in the closed loop controller and tells us when R position is within range of the setpoint. This variable is important for our FSM. When it is set to 1, we calculate a new setpoint. When it is 0, we do not generate a new setpoint. This allows the motor to reach its setpoint before a new one is generated \mbox{\Hypertarget{main_8py_a2710766abdf6f3767409cc7642c71148}\label{main_8py_a2710766abdf6f3767409cc7642c71148}} 
\index{main.py@{main.py}!Rswitch@{Rswitch}}
\index{Rswitch@{Rswitch}!main.py@{main.py}}
\doxysubsubsection{\texorpdfstring{Rswitch}{Rswitch}}
{\footnotesize\ttfamily main.\+Rswitch = \mbox{\hyperlink{classtask__share_1_1Share}{task\+\_\+share.\+Share}} (\textquotesingle{}h\textquotesingle{}, thread\+\_\+protect = False, name = \char`\"{}R\+\_\+\+Switch\char`\"{})}

Shared variable for the value of our R limit switch. 

This variable contains the value of the pin that our limit switch is connected to. We are using this limit switch as a kill switch so that when the pin value changes from 1 to 0, the duty to all our motors is set to 0. This prevents our motors from burning up when the parts reach a mechanical stop. \mbox{\Hypertarget{main_8py_a0f8b18d269c2a71d1bedf53f2ce94c12}\label{main_8py_a0f8b18d269c2a71d1bedf53f2ce94c12}} 
\index{main.py@{main.py}!servopin@{servopin}}
\index{servopin@{servopin}!main.py@{main.py}}
\doxysubsubsection{\texorpdfstring{servopin}{servopin}}
{\footnotesize\ttfamily main.\+servopin = pyb.\+Pin (pyb.\+Pin.\+board.\+PA7, pyb.\+Pin.\+OUT\+\_\+\+PP)}

Variable for the pin our servo motor is connected to. 

This variable sets up our servo motor pin as pin A7 \mbox{\Hypertarget{main_8py_a7b85b2b65758a558f3e3032f3950c355}\label{main_8py_a7b85b2b65758a558f3e3032f3950c355}} 
\index{main.py@{main.py}!setpoint1@{setpoint1}}
\index{setpoint1@{setpoint1}!main.py@{main.py}}
\doxysubsubsection{\texorpdfstring{setpoint1}{setpoint1}}
{\footnotesize\ttfamily main.\+setpoint1 = \mbox{\hyperlink{classtask__share_1_1Share}{task\+\_\+share.\+Share}} (\textquotesingle{}f\textquotesingle{}, thread\+\_\+protect = False, name = \char`\"{}Set\+\_\+\+Point1\char`\"{})}

Shared variable for the setpoint of motor 1. 

This variable is set up as a float so that when we calculate the setpoint from our Gcode, if it has a decimal result, the shared variable structure will allow for that value to be written to it. This variable is written in task1 and is read in our closed loop controller. \mbox{\Hypertarget{main_8py_aaa37d4ce2366d78815bdf5dd79d8cc08}\label{main_8py_aaa37d4ce2366d78815bdf5dd79d8cc08}} 
\index{main.py@{main.py}!setpoint2@{setpoint2}}
\index{setpoint2@{setpoint2}!main.py@{main.py}}
\doxysubsubsection{\texorpdfstring{setpoint2}{setpoint2}}
{\footnotesize\ttfamily main.\+setpoint2 = \mbox{\hyperlink{classtask__share_1_1Share}{task\+\_\+share.\+Share}} (\textquotesingle{}f\textquotesingle{}, thread\+\_\+protect = False, name = \char`\"{}Set\+\_\+\+Point2\char`\"{})}

Shared variable for the setpoint of motor 2. 

This variable is set up as a float so that when we calculate the setpoint from our Gcode, if it has a decimal result, the shared variable structure will allow for that value to be written to it. This variable is written in task1 and is read in our closed loop controller. \mbox{\Hypertarget{main_8py_addd6eb1e79cd691ae9c336b0851e355f}\label{main_8py_addd6eb1e79cd691ae9c336b0851e355f}} 
\index{main.py@{main.py}!switchpin1@{switchpin1}}
\index{switchpin1@{switchpin1}!main.py@{main.py}}
\doxysubsubsection{\texorpdfstring{switchpin1}{switchpin1}}
{\footnotesize\ttfamily main.\+switchpin1 = pyb.\+Pin(pyb.\+Pin.\+board.\+PA8, pyb.\+Pin.\+IN, pyb.\+Pin.\+PULL\+\_\+\+DOWN)}

Variable for the pin our first limit switch is connected to. 

This variable sets up our servo motor pin as pin A8 and uses a pull down resistor to ensure correct output. \mbox{\Hypertarget{main_8py_abde9446db54730de9ad440618259af91}\label{main_8py_abde9446db54730de9ad440618259af91}} 
\index{main.py@{main.py}!switchpin2@{switchpin2}}
\index{switchpin2@{switchpin2}!main.py@{main.py}}
\doxysubsubsection{\texorpdfstring{switchpin2}{switchpin2}}
{\footnotesize\ttfamily main.\+switchpin2 = pyb.\+Pin(pyb.\+Pin.\+board.\+PA6, pyb.\+Pin.\+IN, pyb.\+Pin.\+PULL\+\_\+\+DOWN)}

Variable for the pin our second limit switch is connected to. 

This variable sets up our servo motor pin as pin A6 and uses a pull down resistor to ensure correct output. \mbox{\Hypertarget{main_8py_af4b8f4290f8d32e70654f6deb864787f}\label{main_8py_af4b8f4290f8d32e70654f6deb864787f}} 
\index{main.py@{main.py}!task1@{task1}}
\index{task1@{task1}!main.py@{main.py}}
\doxysubsubsection{\texorpdfstring{task1}{task1}}
{\footnotesize\ttfamily main.\+task1}

{\bfseries Initial value\+:}
\begin{DoxyCode}{0}
\DoxyCodeLine{1 =  \mbox{\hyperlink{classcotask_1_1Task}{cotask.Task}} (task1\_fun, name = \textcolor{stringliteral}{'Task\_1'}, priority = 2,}
\DoxyCodeLine{2                                              period = 200, profile = \textcolor{keyword}{True}, trace = \textcolor{keyword}{False})}

\end{DoxyCode}
\mbox{\Hypertarget{main_8py_a99d189b8f9eb3784cf7d4e5c3241b562}\label{main_8py_a99d189b8f9eb3784cf7d4e5c3241b562}} 
\index{main.py@{main.py}!task2@{task2}}
\index{task2@{task2}!main.py@{main.py}}
\doxysubsubsection{\texorpdfstring{task2}{task2}}
{\footnotesize\ttfamily main.\+task2}

{\bfseries Initial value\+:}
\begin{DoxyCode}{0}
\DoxyCodeLine{1 =  \mbox{\hyperlink{classcotask_1_1Task}{cotask.Task}} (task2\_fun, name = \textcolor{stringliteral}{'Task\_2'}, priority = 3,}
\DoxyCodeLine{2                                              period = 10, profile = \textcolor{keyword}{True}, trace = \textcolor{keyword}{False})}

\end{DoxyCode}
\mbox{\Hypertarget{main_8py_a120516a5d42c212c898d4616d266077a}\label{main_8py_a120516a5d42c212c898d4616d266077a}} 
\index{main.py@{main.py}!task3@{task3}}
\index{task3@{task3}!main.py@{main.py}}
\doxysubsubsection{\texorpdfstring{task3}{task3}}
{\footnotesize\ttfamily main.\+task3}

{\bfseries Initial value\+:}
\begin{DoxyCode}{0}
\DoxyCodeLine{1 =  \mbox{\hyperlink{classcotask_1_1Task}{cotask.Task}} (task3\_fun, name = \textcolor{stringliteral}{'Task\_3'}, priority = 2,}
\DoxyCodeLine{2                                             period = 40, profile = \textcolor{keyword}{True}, trace = \textcolor{keyword}{False})}

\end{DoxyCode}
\mbox{\Hypertarget{main_8py_a8c2153a050d8d0173f8bb43ef99e7174}\label{main_8py_a8c2153a050d8d0173f8bb43ef99e7174}} 
\index{main.py@{main.py}!THETAGO@{THETAGO}}
\index{THETAGO@{THETAGO}!main.py@{main.py}}
\doxysubsubsection{\texorpdfstring{THETAGO}{THETAGO}}
{\footnotesize\ttfamily main.\+THETAGO = \mbox{\hyperlink{classtask__share_1_1Share}{task\+\_\+share.\+Share}} (\textquotesingle{}h\textquotesingle{}, thread\+\_\+protect = False, name = \char`\"{}THETAGO\char`\"{})}

Shared variable to tell us when theta is ready to move. 

This variable is calculated in the closed loop controller and tells us when theta position is within range of the setpoint. This variable is important for our FSM. When it is set to 1, we calculate a new setpoint. When it is 0, we do not generate a new setpoint. This allows the motor to reach its setpoint before a new one is generated. \mbox{\Hypertarget{main_8py_ac3ee7e26a582192f6abba62394fd964d}\label{main_8py_ac3ee7e26a582192f6abba62394fd964d}} 
\index{main.py@{main.py}!zpos@{zpos}}
\index{zpos@{zpos}!main.py@{main.py}}
\doxysubsubsection{\texorpdfstring{zpos}{zpos}}
{\footnotesize\ttfamily main.\+zpos = \mbox{\hyperlink{classtask__share_1_1Share}{task\+\_\+share.\+Share}} (\textquotesingle{}h\textquotesingle{}, thread\+\_\+protect = False, name = \char`\"{}z\+\_\+\+Position\char`\"{})}

Shared variable for the z position for our half axis. 

This variable is either 0 or 1 depending on if we want our servo motor to be down or up. This allows us to raise and lower our Sharpie for tracing the correct contours.

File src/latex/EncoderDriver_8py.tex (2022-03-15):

\hypertarget{EncoderDriver_8py}{}\doxysection{Encoder\+Driver.\+py File Reference}
\label{EncoderDriver_8py}\index{EncoderDriver.py@{EncoderDriver.py}}

This file provides the code to interface directly with the encoder hardware.  

\doxysubsection*{Classes}
\begin{DoxyCompactItemize}
\item 
class \mbox{\hyperlink{classEncoderDriver_1_1EncoderDriver}{Encoder\+Driver.\+Encoder\+Driver}}
\begin{DoxyCompactList}\small\item\em Interface with quadrature encoders. \end{DoxyCompactList}\end{DoxyCompactItemize}
\doxysubsection*{Variables}
\begin{DoxyCompactItemize}
\item 
\mbox{\Hypertarget{EncoderDriver_8py_a31b5d4a9787f0f44826c36aa9ed5ac04}\label{EncoderDriver_8py_a31b5d4a9787f0f44826c36aa9ed5ac04}} 
{\bfseries Encoder\+Driver.\+ENCpin1} = pyb.\+Pin (pyb.\+Pin.\+board.\+PC6)
\item 
\mbox{\Hypertarget{EncoderDriver_8py_a0df7699970f6cb09e3b6ba0ed2054940}\label{EncoderDriver_8py_a0df7699970f6cb09e3b6ba0ed2054940}} 
{\bfseries Encoder\+Driver.\+ENCpin2} = pyb.\+Pin (pyb.\+Pin.\+board.\+PC7)
\item 
\mbox{\Hypertarget{EncoderDriver_8py_ad9339a5123c3856bf85c2e1726c99bcf}\label{EncoderDriver_8py_ad9339a5123c3856bf85c2e1726c99bcf}} 
int {\bfseries Encoder\+Driver.\+timernumber} = 8
\item 
\mbox{\Hypertarget{EncoderDriver_8py_af176152316dc5932bdfff9fc4e5e4e11}\label{EncoderDriver_8py_af176152316dc5932bdfff9fc4e5e4e11}} 
{\bfseries Encoder\+Driver.\+ENC1} = Encoder\+Driver(ENCpin1,ENCpin2,timernumber)
\end{DoxyCompactItemize}

\doxysubsection{Detailed Description}
This file provides the code to interface directly with the encoder hardware. 

\begin{DoxyAuthor}{Author}
Daniel Gonzalez 

Nolan Clapp 

Caleb Kephart 
\end{DoxyAuthor}
\begin{DoxyDate}{Date}
January 24, 2022 
\end{DoxyDate}

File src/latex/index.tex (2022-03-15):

\hypertarget{index_sec_intro}{}\doxysection{ME 405 Term Project Software Description}\label{index_sec_intro}
This is our project main page for the ME 405 plotter project, and the progress we have made up to this point on the software side of the project.

Our Source Code Repository can be found\+: \hypertarget{index_sec_lb1}{}\doxysection{Task Diagram and File Structure}\label{index_sec_lb1}
We developed the Task Diagram seen below to demonstrate the file structure that we plan to use in our 2.\+5D plotter. Each of the files will have some combination of shares and/or queues in order to allow for variable data to be shared between files. The exact shares between files is shown in the diagram. We will utilize this by using the Task\+\_\+\+Shares.\+py file that we have been provided to ensure the shared variables are set up correctly, and contain usable data. In addition, we plan to have the differnet tasks communicate with eachother using the structure outlined in previous labs and by using Co\+Tasks.\+py to make sure we are taking advantage of cooperative multitasking. To simplify what is going on in each of our files, we are only using FSMs at the task level. We have one for task2 Motor\+Control Task and task3 Servo\+Motor Task. These diagrams are shown in \mbox{\hyperlink{ThetaMotorControl_8py}{Theta\+Motor\+Control.\+py}} and \mbox{\hyperlink{RMotorControl_8py}{RMotor\+Control.\+py}} and \mbox{\hyperlink{ServoMotorF_8py}{Servo\+Motor\+F.\+py}} sections respectively.

The files that we are using\+: ~\newline
 main Main file that runs all of our tasks and instantiates all objects ~\newline
 Encoder\+Driver Read the position of the Theta Motor ~\newline
 Encoder Read the position of the R Motor ~\newline
 Motor\+Driver Control the motor by supplying a duty ~\newline
 Theta\+Motor\+Control Closed loop control of Theta Motor ~\newline
 RMotor\+Control Closed loop control of R Motor ~\newline
 Servo\+MotorF Control the servo motor responsible for our half axis as well as limit switch reading ~\newline
 Gcode\+Interpreter Writed R and Theta Setpoints to .txt file to be read later ~\newline

The Task Diagram showing how these files are used is shown below.

The frist image shows the Overall Task Diagram that is running in our system, and the second shows the subtasks that are running inside of each task. We are running 3 tasks, each represented by a different color box, Blue is task1, Red is task2, and Green is task3. If there are multiple boxes of the same color, they are treated as subtasks. Each of this subtasks and their shares is shown in the second picture. Each of the shares we are using is represented with a dashed line pointing from where the variable is written to where the variable is read. We chose to split the task diagram up this way so that it better demonstrated what is happening with each share.

The procedure on how we used our code is shown below\+:
\begin{DoxyEnumerate}
\item Create GCODE using \href{http://jscut.org/jscut.html\#}{\texttt{ http\+://jscut.\+org/jscut.\+html\#}} by converting a .SVG to tool paths
\item Save the .gcode file that was created as NAME.\+txt
\item Run NAME.\+text through \mbox{\hyperlink{GcodeInterpreter_8py}{Gcode\+Interpreter.\+py}} to output text files for desired R and Theta motor angles
\item Save all necessary files on the Nucleo
\item Run \mbox{\hyperlink{main_8py}{main.\+py}} on the Nucleo to use the plotter ~\newline
 a. \mbox{\hyperlink{main_8py}{main.\+py}} uses \mbox{\hyperlink{cotask_8py}{cotask.\+py}} for cooperative multitasking. ~\newline
 b. Task1 generates the setpoint for both motors ~\newline
 c. Task2 calculates encoder position, runs closed loop controller, and runs motor driver with duty from the controller ~\newline
 d. Task3 controls the servo motor. If we want to draw, Zpos=1, if we want to lift, Zpos=0 ~\newline
 e. Repeat running all tasks until the ends of the setpoint text files are reached ~\newline

\end{DoxyEnumerate}\hypertarget{index_sec_lb2}{}\doxysection{main.\+py}\label{index_sec_lb2}
This file is the starting point of all of our software. We set up all needed hardware to software interface (pins and timers), set up our shared variables, and instantiate all objects. This file also contains the generator responsibile for running all of our tsaks cooperatively.\hypertarget{index_sec_lb3}{}\doxysection{Encoder\+Driver.\+py and Encoder.\+py}\label{index_sec_lb3}
These two files are very similar, the only differnece is that \mbox{\hyperlink{EncoderDriver_8py}{Encoder\+Driver.\+py}} reads the Theta encoder and Encoder.\+py reads only the R encoder. These files are only used to calculate encoder position. When we read the encoder position, we write that value to a shared variable for each position. For Theta\+Encoder\+Position.\+write(\+Encoder\+Position). We calcualte this encoder position by calculating the encoder delta from a timer on the microcontroller and the previous time. This allows us to calculate encoder position without worrying about the encoder \char`\"{}overflowing,\char`\"{} where the encoder position essentially resets to 0 once the reading reaches 65535. We decided to split \mbox{\hyperlink{EncoderDriver_8py}{Encoder\+Driver.\+py}} and Encoder.\+py to make it easy to troubleshoot any errors that may come up. Origionally, \mbox{\hyperlink{EncoderDriver_8py}{Encoder\+Driver.\+py}} was responsible for reading both encoder positions, so that is why it has R encoder pins, timer, and shares passed into the class, but they are never used. Similarly, since we only need R motor stuff passed into Encoder, we changed that file to only have necessary values shared to that file. In short, instead of changing \mbox{\hyperlink{EncoderDriver_8py}{Encoder\+Driver.\+py}} from its origional state, we left it as is, and created a single copy that would only be used for the R motor and deleted all information related to the Theta motor.\hypertarget{index_sec_lb4}{}\doxysection{Motor\+Driver.\+py}\label{index_sec_lb4}
This file is responsible for taking the duty input from other files and making the motors turn at that duty. Once the motor driver is instantiated, the methodd that are called repeatidly are set\+\_\+duty\+\_\+cycle and set\+\_\+duty\+\_\+cycle2 (one for R motor and 1 for Theta motor). These methods enable the motor by setting the enable pin to high, and also sets both output pins to low. We then set the duty by changing the PWM \% to the desired duty value. If the desired duty is positive, we set the PWM duty cycle of channel1, but if it is negative, e set the PWM duty cycle of channel2. The pin that does not have the duty cycle applied to it is set to a duty of 0. Example (Positive duty-\/\texorpdfstring{$>$}{>} CH1.\+pule\+\_\+width\+\_\+percent(\+DUTY) and CH2.\+pule\+\_\+width\+\_\+percent(0))\hypertarget{index_sec_lb5}{}\doxysection{Theta\+Motor\+Control.\+py and RMotor\+Control.\+py}\label{index_sec_lb5}
These two files are responsible for all of our closed loop system control. We are using a simple porportional controller with gain Kp. The control loop that is run over and over calculated the error signal (error=setpoint-\/\+Encoder\+Position), multiplies that by gain, Kp, and then sets the duty to this value, called the actuation signal. This file is necessary to determine when our motor reaches the desired position. In addition, these files determine when motor position gets within an acceptable range. Once this happens, we set a buffer variable to true so that our code konws when it should generate a new setpoint.

The FSM for the Motor Tasks (including \mbox{\hyperlink{EncoderDriver_8py}{Encoder\+Driver.\+py}}, Control Loops, and \mbox{\hyperlink{MotorDriver_8py}{Motor\+Driver.\+py}}) is shown below. \hypertarget{index_sec_lb6}{}\doxysection{Servo\+Motor\+F.\+py}\label{index_sec_lb6}
This file is responsible for controling our servo motor and limit switch. We have classes for both the servo motor, and the limit switch. The servo motor class contains methods to raise and lower the servo motor called up() and down(). These methods are called in main when a certain Zpos variable changes value. For example, when Zpos=1, the servo motor will move down.

The limit switch class is responsible for reading the value output by the limit switch pins. This is done in the method checkswitch(). This checks the value of the pin using the .value call for the pin. Since the switch was wired to be normally closed, when there is nothing pressing the switch, pin.\+value()=1, but when it is pressed, pin.\+value()=0. We are using this limit switch as a kill switch, so when the value of the pin is 0, we set the duty of the R motor to 0 to prevent the hardware from tearing itself apart.

The FSM for this file is shown below \hypertarget{index_sec_lb7}{}\doxysection{Gcode\+Interpreter.\+py}\label{index_sec_lb7}
In order to generate the path that the pen should take, we used \href{http://jscut.org/jscut.html\#}{\texttt{ http\+://jscut.\+org/jscut.\+html\#}} , a website that accepts SVG images and converts it to GCODE. This website was nice, because each of the GCODE lines were G1, which is the call for a straight line. The GCODE that this website outputs is a series of straight lines that are very short (around 0.\+001"{}). This means, we essentially have a list of X-\/Y coordinates that trace out our image.

We then use the file \mbox{\hyperlink{GcodeInterpreter_8py}{Gcode\+Interpreter.\+py}}, to take each line of GCODE, pull out the desired X-\/Y coordinates, and then preform some math to convert these to R-\/\+Theta coordinates. From these R-\/\+Theta coordinates, we use our known gear ratios to write the desired R Motor angle and Theta Motor angle to their own .txt files.

We then read each line of these files in \mbox{\hyperlink{main_8py}{main.\+py}} to get the setpoint of both motors. This is only done when the motor has reached its previous setpoint and the buffer variable is set to 1.

\begin{DoxyAuthor}{Author}
Nolan Clapp 

Caleb Kephart 

Daniel Gonzalez 
\end{DoxyAuthor}
\begin{DoxyDate}{Date}
Feb 22, 2022 
\end{DoxyDate}

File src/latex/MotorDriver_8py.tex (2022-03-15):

\hypertarget{MotorDriver_8py}{}\doxysection{Motor\+Driver.\+py File Reference}
\label{MotorDriver_8py}\index{MotorDriver.py@{MotorDriver.py}}

A driver file for interacting with motors.  

\doxysubsection*{Classes}
\begin{DoxyCompactItemize}
\item 
class \mbox{\hyperlink{classMotorDriver_1_1MotorDriver}{Motor\+Driver.\+Motor\+Driver}}
\begin{DoxyCompactList}\small\item\em This class implements a motor driver for an ME405 kit. \end{DoxyCompactList}\end{DoxyCompactItemize}
\doxysubsection*{Variables}
\begin{DoxyCompactItemize}
\item 
\mbox{\Hypertarget{MotorDriver_8py_a17cb3058c58ebc54e6001d414730b2f2}\label{MotorDriver_8py_a17cb3058c58ebc54e6001d414730b2f2}} 
{\bfseries Motor\+Driver.\+en\+\_\+pin} = pyb.\+Pin (pyb.\+Pin.\+board.\+PC0, pyb.\+Pin.\+OUT\+\_\+\+PP)
\item 
\mbox{\Hypertarget{MotorDriver_8py_a5a2c52f0fc0bad9284f9a9df8794282f}\label{MotorDriver_8py_a5a2c52f0fc0bad9284f9a9df8794282f}} 
{\bfseries Motor\+Driver.\+in1pin} = pyb.\+Pin (pyb.\+Pin.\+board.\+PA0, pyb.\+Pin.\+OUT\+\_\+\+PP)
\item 
\mbox{\Hypertarget{MotorDriver_8py_a64ae348ab71ac272271b4a90caec19f7}\label{MotorDriver_8py_a64ae348ab71ac272271b4a90caec19f7}} 
{\bfseries Motor\+Driver.\+in2pin} = pyb.\+Pin (pyb.\+Pin.\+board.\+PA1, pyb.\+Pin.\+OUT\+\_\+\+PP)
\item 
\mbox{\Hypertarget{MotorDriver_8py_a5666aeae7802c073d246a597a5ec74d8}\label{MotorDriver_8py_a5666aeae7802c073d246a597a5ec74d8}} 
int {\bfseries Motor\+Driver.\+timer} = 3
\item 
\mbox{\Hypertarget{MotorDriver_8py_a7cc6c65363fe943d1d0e4379bac398d0}\label{MotorDriver_8py_a7cc6c65363fe943d1d0e4379bac398d0}} 
{\bfseries Motor\+Driver.\+motor1} = Motor\+Driver(en\+\_\+pin, in1pin, in2pin, timer)
\end{DoxyCompactItemize}

\doxysubsection{Detailed Description}
A driver file for interacting with motors. 

This driver file interacts with motors by sending duty cycle values and setting pin values to control the motor behavior.

\begin{DoxyAuthor}{Author}
Daniel Gonzalez 

Nolan Clapp 

Caleb Kephart 
\end{DoxyAuthor}
\begin{DoxyDate}{Date}
January 24, 2022 
\end{DoxyDate}

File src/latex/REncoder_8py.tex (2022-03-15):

\hypertarget{REncoder_8py}{}\doxysection{REncoder.\+py File Reference}
\label{REncoder_8py}\index{REncoder.py@{REncoder.py}}

This file provides the code to interface directly with the encoder2 hardware.  

\doxysubsection*{Classes}
\begin{DoxyCompactItemize}
\item 
class \mbox{\hyperlink{classREncoder_1_1EncoderDriver}{REncoder.\+Encoder\+Driver}}
\begin{DoxyCompactList}\small\item\em Interface with quadrature encoders. \end{DoxyCompactList}\end{DoxyCompactItemize}
\doxysubsection*{Variables}
\begin{DoxyCompactItemize}
\item 
\mbox{\Hypertarget{REncoder_8py_a5fc27bf045e1c49bf2635491b82288d1}\label{REncoder_8py_a5fc27bf045e1c49bf2635491b82288d1}} 
{\bfseries REncoder.\+ENCpin1} = pyb.\+Pin (pyb.\+Pin.\+board.\+PC6)
\item 
\mbox{\Hypertarget{REncoder_8py_a2808c9962f9f56aebead3862ce701401}\label{REncoder_8py_a2808c9962f9f56aebead3862ce701401}} 
{\bfseries REncoder.\+ENCpin2} = pyb.\+Pin (pyb.\+Pin.\+board.\+PC7)
\item 
\mbox{\Hypertarget{REncoder_8py_aa7dcb62d9578f4fa2495e41df04356f4}\label{REncoder_8py_aa7dcb62d9578f4fa2495e41df04356f4}} 
int {\bfseries REncoder.\+timernumber} = 8
\item 
\mbox{\Hypertarget{REncoder_8py_a46aca80a45b6ef507a9c852a3732cde8}\label{REncoder_8py_a46aca80a45b6ef507a9c852a3732cde8}} 
{\bfseries REncoder.\+ENC1} = Encoder\+Driver(ENCpin1,ENCpin2,timernumber)
\end{DoxyCompactItemize}

\doxysubsection{Detailed Description}
This file provides the code to interface directly with the encoder2 hardware. 

\begin{DoxyAuthor}{Author}
Daniel Gonzalez 

Nolan Clapp 

Caleb Kephart 
\end{DoxyAuthor}
\begin{DoxyDate}{Date}
January 24, 2022 
\end{DoxyDate}

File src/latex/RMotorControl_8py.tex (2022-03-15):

\hypertarget{RMotorControl_8py}{}\doxysection{RMotor\+Control.\+py File Reference}
\label{RMotorControl_8py}\index{RMotorControl.py@{RMotorControl.py}}

This file provides the code to run closed loop control on R motor.  

\doxysubsection*{Classes}
\begin{DoxyCompactItemize}
\item 
class \mbox{\hyperlink{classRMotorControl_1_1RClosedLoop}{RMotor\+Control.\+RClosed\+Loop}}
\begin{DoxyCompactList}\small\item\em Puts system into a closed loop. \end{DoxyCompactList}\end{DoxyCompactItemize}

\doxysubsection{Detailed Description}
This file provides the code to run closed loop control on R motor. 

\begin{DoxyAuthor}{Author}
Daniel Gonzalez 

Nolan Clapp 

Caleb Kephart 
\end{DoxyAuthor}
\begin{DoxyDate}{Date}
March 8, 2022 
\end{DoxyDate}

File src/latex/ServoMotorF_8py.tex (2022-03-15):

\hypertarget{ServoMotorF_8py}{}\doxysection{Servo\+Motor\+F.\+py File Reference}
\label{ServoMotorF_8py}\index{ServoMotorF.py@{ServoMotorF.py}}

This file for interacting with a servo motor and a limit switch.  

\doxysubsection*{Classes}
\begin{DoxyCompactItemize}
\item 
class \mbox{\hyperlink{classServoMotorF_1_1ServoMotorF}{Servo\+Motor\+F.\+Servo\+MotorF}}
\begin{DoxyCompactList}\small\item\em This class implements a driver to control a servo motor. \end{DoxyCompactList}\item 
class \mbox{\hyperlink{classServoMotorF_1_1LimitSwitch}{Servo\+Motor\+F.\+Limit\+Switch}}
\begin{DoxyCompactList}\small\item\em This class initializes a limit switch used on the R motor. \end{DoxyCompactList}\end{DoxyCompactItemize}
\doxysubsection*{Variables}
\begin{DoxyCompactItemize}
\item 
\mbox{\Hypertarget{ServoMotorF_8py_a8282c10220e82f102ad1b17e86c5682d}\label{ServoMotorF_8py_a8282c10220e82f102ad1b17e86c5682d}} 
{\bfseries Servo\+Motor\+F.\+pin\+A8} = pyb.\+Pin(pyb.\+Pin.\+board.\+PA8, pyb.\+Pin.\+IN, pyb.\+Pin.\+PULL\+\_\+\+DOWN)
\end{DoxyCompactItemize}

\doxysubsection{Detailed Description}
This file for interacting with a servo motor and a limit switch. 

This driver file interacts with servo motor by sending a PWM signal through a set pin. The positioning of the servo motor is controlled by the PWM signal. \begin{DoxyAuthor}{Author}
Daniel Gonzalez 

Nolan Clapp 

Caleb Kephart 
\end{DoxyAuthor}
\begin{DoxyDate}{Date}
Feburary 22, 2022 
\end{DoxyDate}

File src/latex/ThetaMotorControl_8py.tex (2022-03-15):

\hypertarget{ThetaMotorControl_8py}{}\doxysection{Theta\+Motor\+Control.\+py File Reference}
\label{ThetaMotorControl_8py}\index{ThetaMotorControl.py@{ThetaMotorControl.py}}

This file provides the code to run closed loop control on Theta motor.  

\doxysubsection*{Classes}
\begin{DoxyCompactItemize}
\item 
class \mbox{\hyperlink{classThetaMotorControl_1_1ThetaClosedLoop}{Theta\+Motor\+Control.\+Theta\+Closed\+Loop}}
\begin{DoxyCompactList}\small\item\em Puts system into a closed loop. \end{DoxyCompactList}\end{DoxyCompactItemize}

\doxysubsection{Detailed Description}
This file provides the code to run closed loop control on Theta motor. 

\begin{DoxyAuthor}{Author}
Daniel Gonzalez 

Nolan Clapp 

Caleb Kephart 
\end{DoxyAuthor}
\begin{DoxyDate}{Date}
March 8, 2022 
\end{DoxyDate}

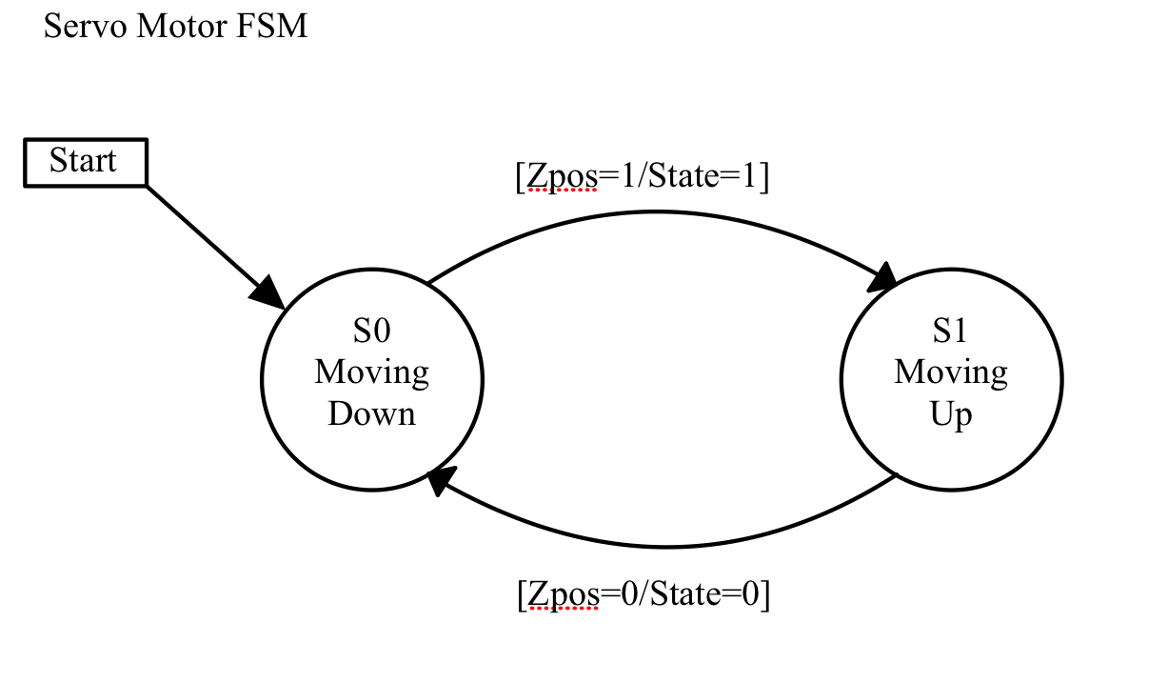
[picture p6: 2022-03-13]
docs/ServoFSM.png

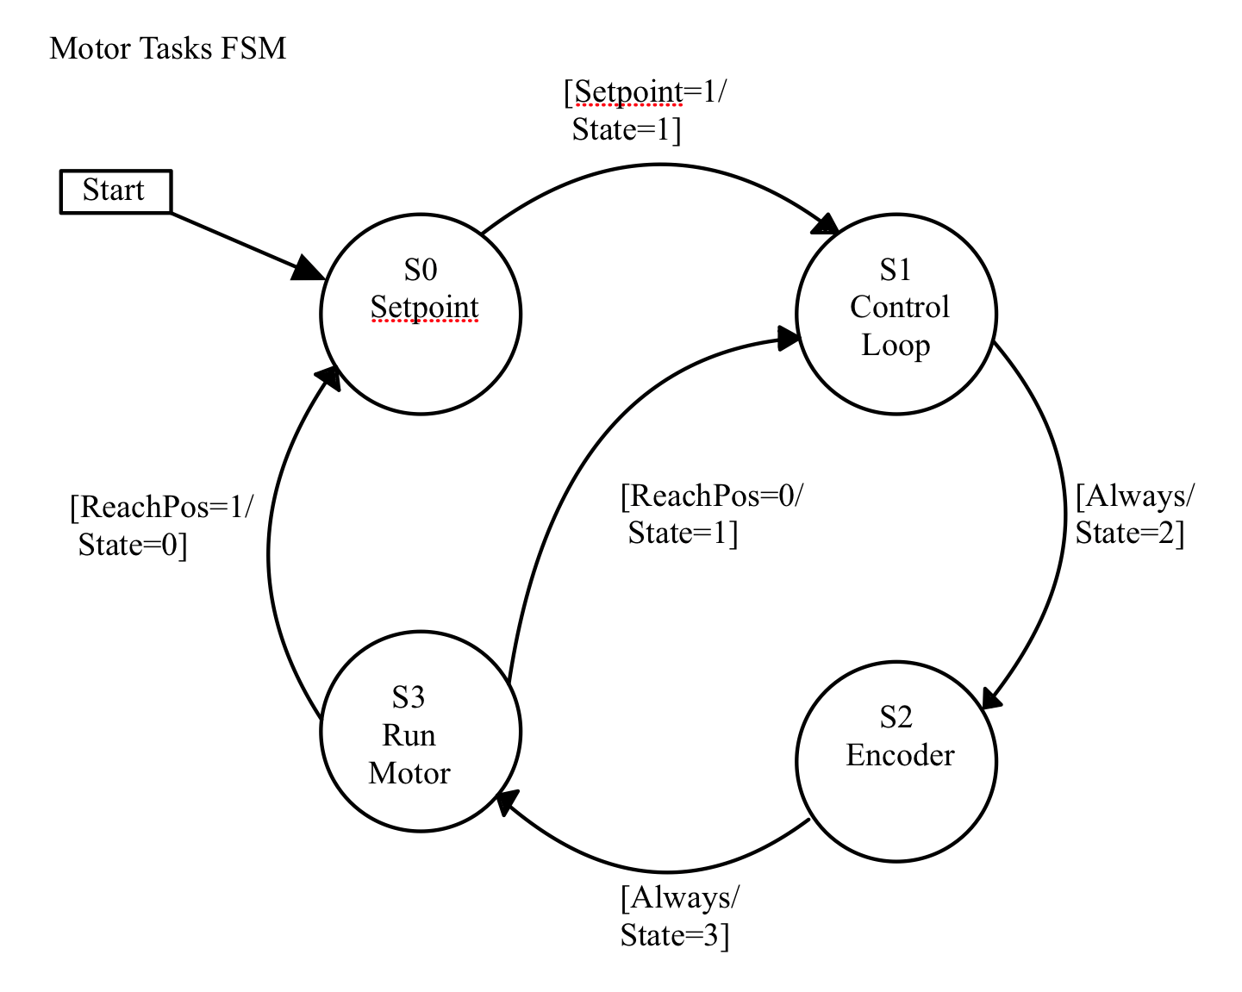
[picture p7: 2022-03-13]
docs/MotorControlFSM.png

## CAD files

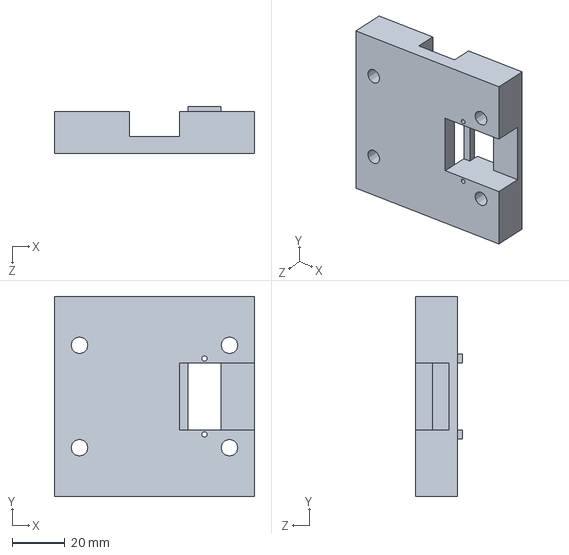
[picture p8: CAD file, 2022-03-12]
TP CAD/maincar.SLDPRT
76.2 x 76.2 x 17.8 mm

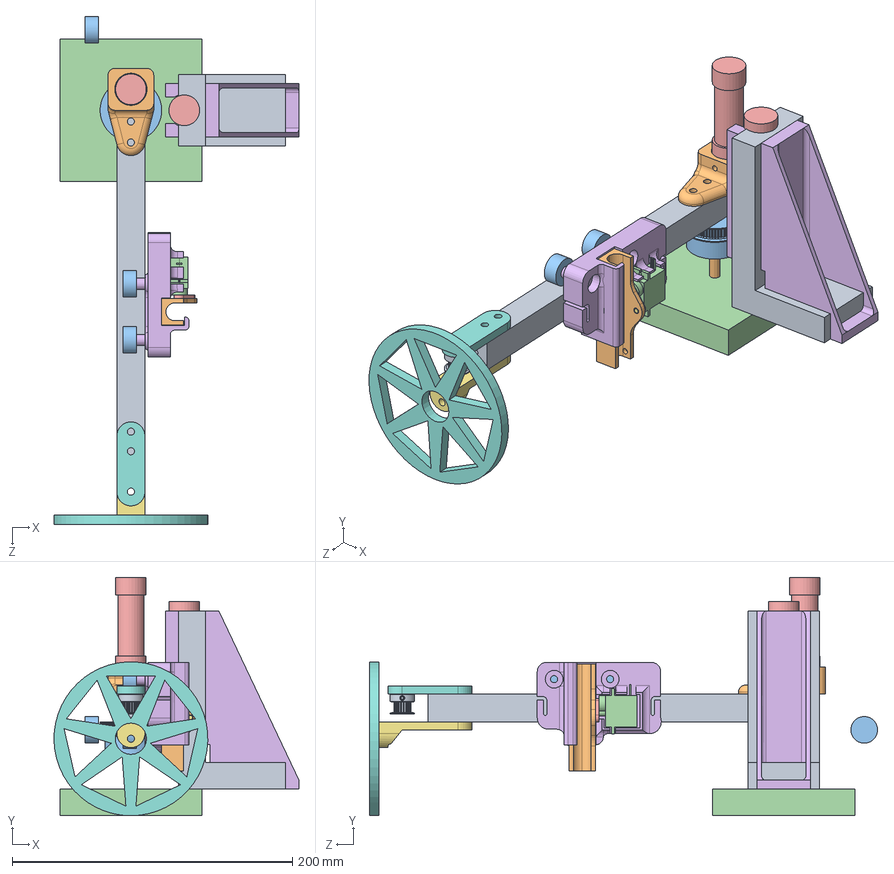
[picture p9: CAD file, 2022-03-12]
TP CAD/MainCarAssem.SLDASM
174.9 x 170.2 x 362.8 mm
Sharpiecar
VBear x 3
ServoMotor
L
BackPlateUpdated
pin3
Pully Mount
MotorPully x 3
RMotorMount
60TPulley
Base
PittmanMotor x 2
ThetaMotorMount
Pully Mount and Wheel
Wheel
Shaft

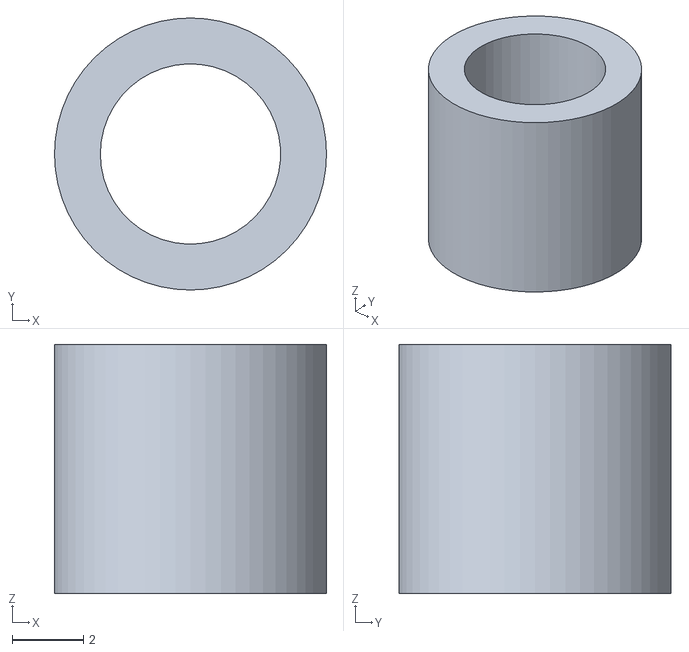
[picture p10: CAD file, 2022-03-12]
TP CAD/bearingM5con.STL
7.62 x 7.62 x 6.98

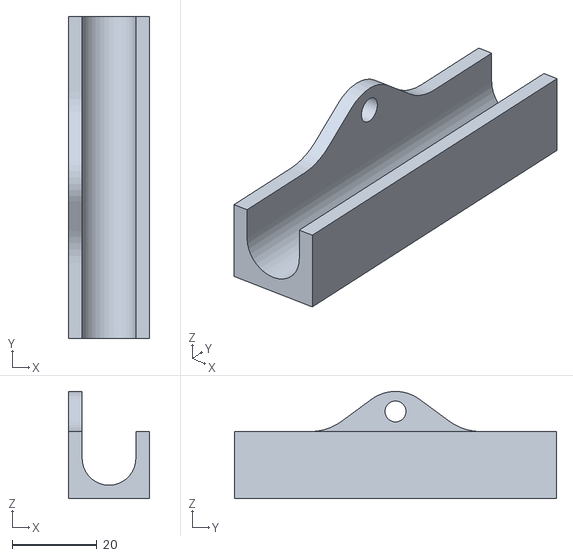
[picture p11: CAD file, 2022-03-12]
TP CAD/To Print/Sharpiecar.STL
19.1 x 76.2 x 25.4

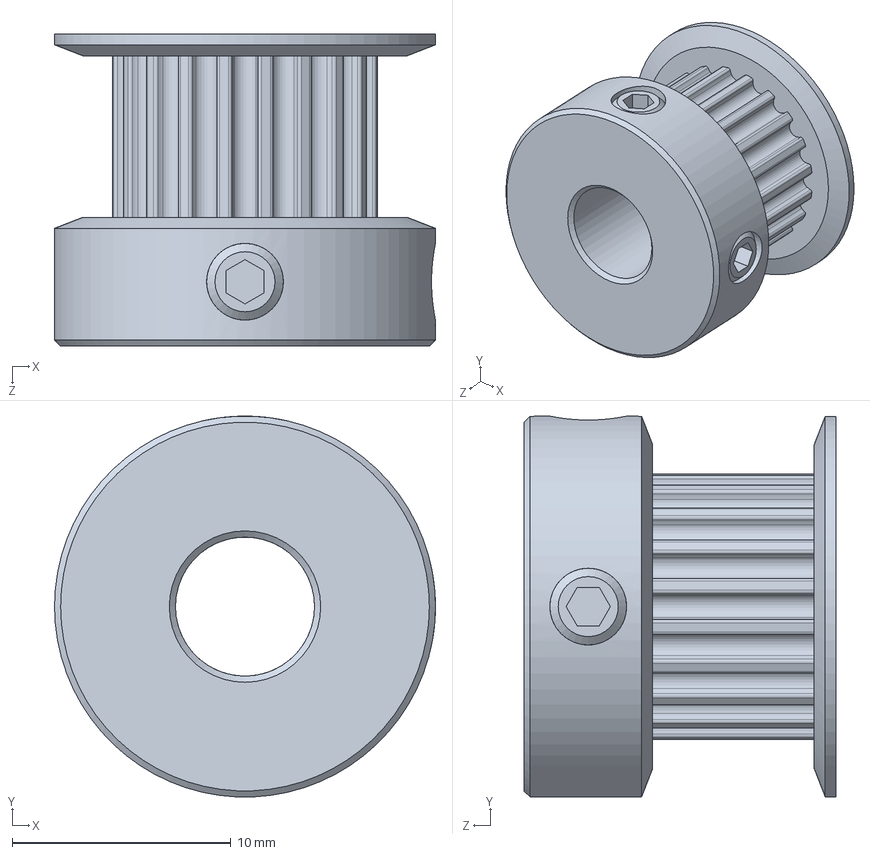
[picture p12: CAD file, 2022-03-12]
TP CAD/MotorPully.SLDPRT
17.4 x 17.4 x 14.3 mm

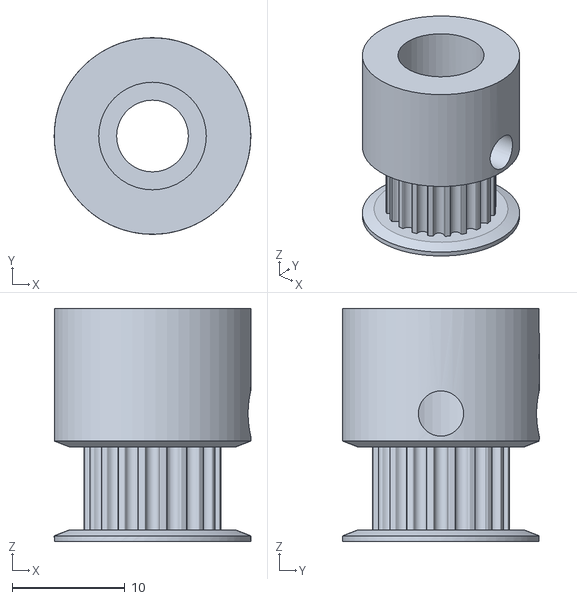
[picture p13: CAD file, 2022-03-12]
TP CAD/To Print/Pully.STL
17.4 x 17.4 x 20.6

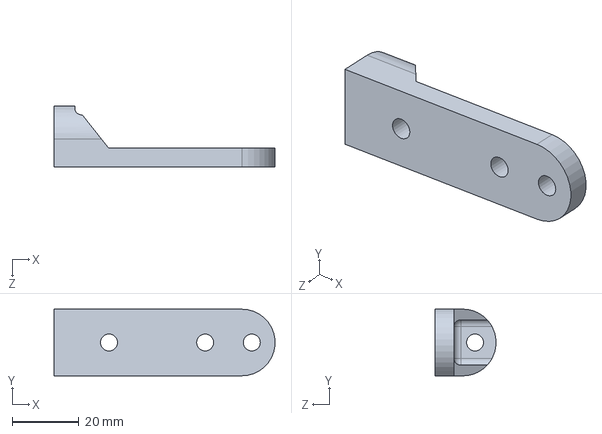
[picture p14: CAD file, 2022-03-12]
TP CAD/Pully Mount and Wheel.SLDPRT
66.3 x 20.0 x 18.3 mm

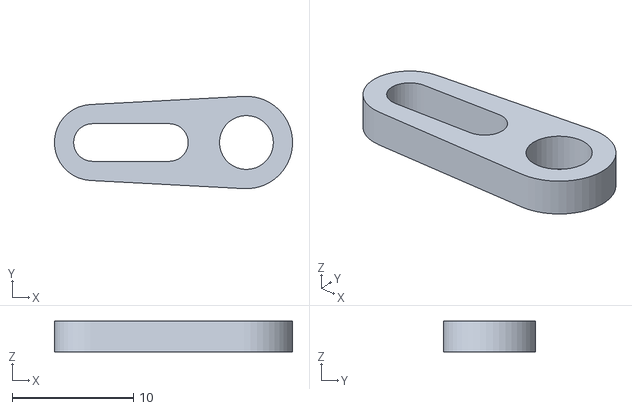
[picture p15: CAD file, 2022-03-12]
TP CAD/To Print/L.STL
19.6 x 7.61 x 2.54

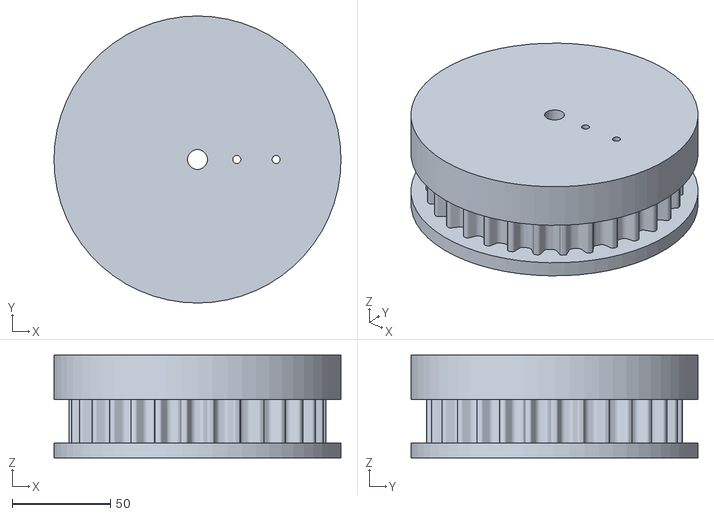
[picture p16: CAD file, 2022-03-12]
TP CAD/To Print/Big Pulley.STL
146.0 x 146.0 x 52.3

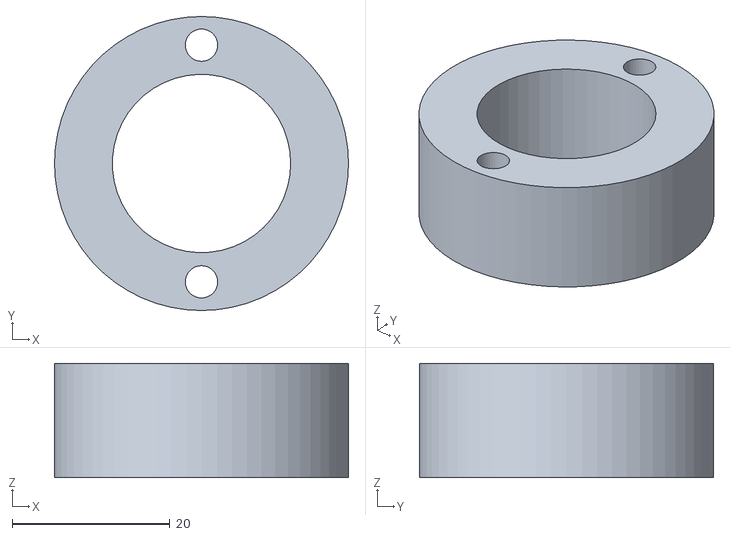
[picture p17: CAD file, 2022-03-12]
TP CAD/To Print/60TPulleyBearingBlock.STL
37.3 x 37.3 x 14.5

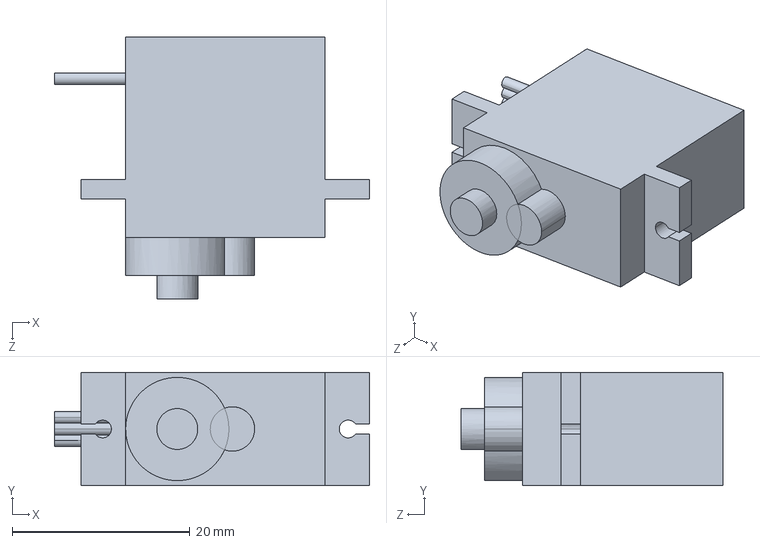
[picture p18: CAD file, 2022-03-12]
TP CAD/ServoMotor.SLDPRT
35.4 x 12.7 x 29.4 mm

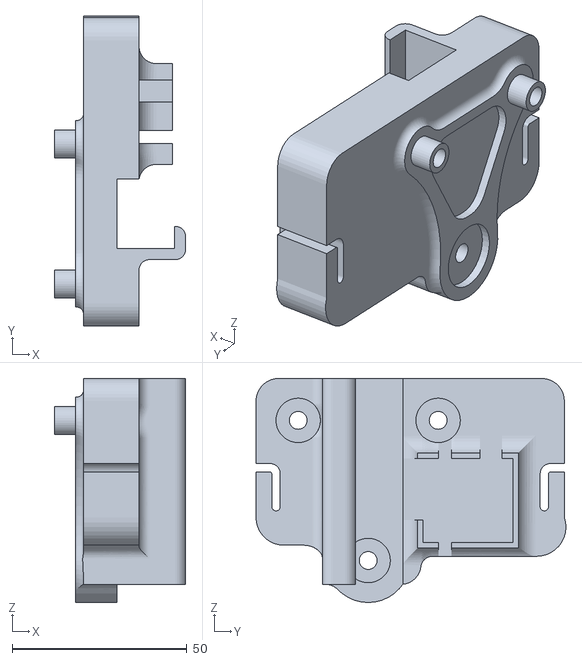
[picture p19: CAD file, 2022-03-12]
TP CAD/To Print/BackPlateUpdated.STL
37.6 x 88.6 x 64.0

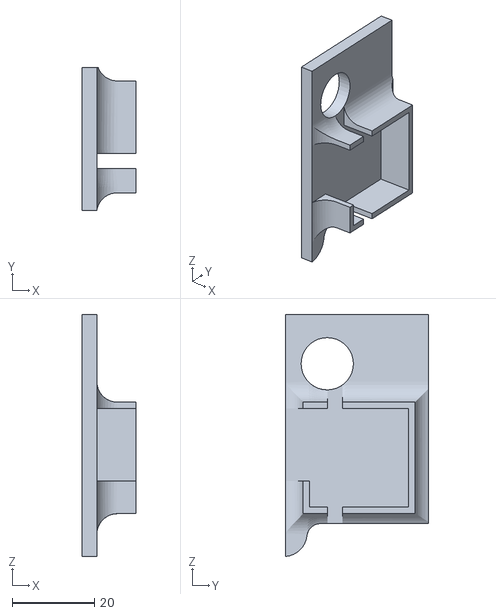
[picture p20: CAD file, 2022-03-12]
TP CAD/To Print/ServoFit.STL
13.2 x 34.6 x 58.8

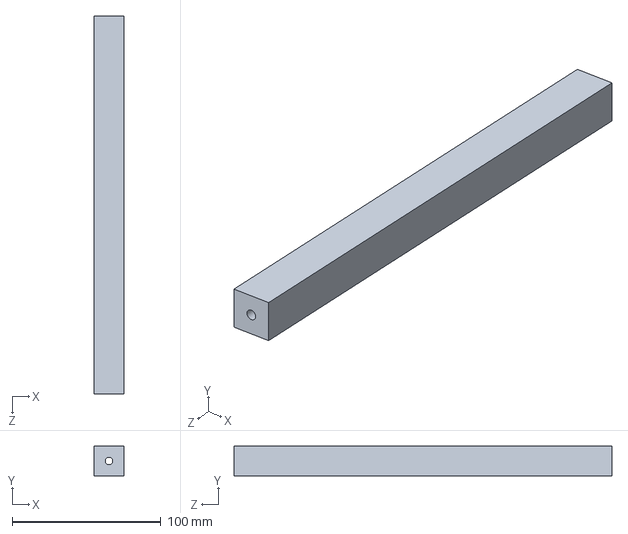
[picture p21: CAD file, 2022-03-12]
TP CAD/2020.SLDPRT
20.0 x 20.0 x 254.0 mm

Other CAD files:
TP CAD/Shaft.SLDPRT
TP CAD/Pin.SLDPRT
TP CAD/To Print/ThetaMotorMount.STL
TP CAD/60TPulleyBearingBlock.SLDPRT
TP CAD/60TPulley.SLDPRT
TP CAD/BackPlateUpdated.SLDPRT
TP CAD/Base.SLDPRT
TP CAD/Big Pulley.SLDPRT
TP CAD/L.SLDPRT
TP CAD/MotorMountBrackets.SLDPRT
TP CAD/Pin2.SLDPRT
TP CAD/PittmanMotor.SLDPRT
TP CAD/Pully Mount.SLDPRT
TP CAD/RMotorMount.SLDPRT
TP CAD/Sharpiecar.SLDPRT
TP CAD/ThetaMotorMount.SLDPRT
TP CAD/ThetaPlateMount.SLDPRT
TP CAD/To Print/60TPulley.STL
TP CAD/To Print/Pully Mount and Wheel.STL
TP CAD/To Print/Pully Mount.STL
TP CAD/To Print/RMotorMount - RMotorMount-1.STL
TP CAD/To Print/SharpiecarV2.STL
TP CAD/To Print/Wheel.STL
TP CAD/To Print/WheelV2.STL
TP CAD/To Print/testPully.STL
TP CAD/VBear.SLDPRT
TP CAD/Wheel.SLDPRT
TP CAD/bearingM5convert.SLDPRT
TP CAD/pin3.SLDPRT

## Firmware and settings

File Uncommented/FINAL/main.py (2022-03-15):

"""
    @file                    main.py
    @author                  Daniel Gonzalez
    @author                  Nolan Clapp
    @author                  Caleb Kephart
    @date                    February 7, 2022
"""

import gc
import pyb
import cotask
import task_share
import EncoderDriver
import REncoder
import MotorDriver
import ThetaMotorControl
import RMotorControl
import ServoMotorF
import time

# MOTOR PIN STUFF
#Motor 1, Theta
## @brief This variable is for the enable pin for motor 1
#  @details This variable is responsible for holding the pin information for the pin that 
#           will enable motor 1 when it is set to high. The pin is Pin A10. 
en_pin=pyb.Pin (pyb.Pin.board.PA10, pyb.Pin.OUT_PP)
## @brief This variable is for the first pin of motor 1
#  @details This variable is set to Pin B4, the first pin on the Neucleo for motor 1.
#           This pin is set as an output. 
in1pin=pyb.Pin (pyb.Pin.board.PB4, pyb.Pin.OUT_PP)
## @brief This variable is for the second pin of motor 1
#  @details This variable is set to Pin B5, the first pin on the Neucleo for motor 1.
#           This pin is set as an output. 
in2pin=pyb.Pin (pyb.Pin.board.PB5, pyb.Pin.OUT_PP)
## @brief This variable is for the timer number associated with motor 1
timer=3

#Motor 2, R
## @brief This variable is for the enable pin for motor 2
#  @details This variable is responsible for holding the pin information for the pin that 
#           will enable motor 2 when it is set to high. The pin is Pin C1. 
en_pin2=pyb.Pin (pyb.Pin.board.PC1, pyb.Pin.OUT_PP)
## @brief This variable is for the first pin of motor 2
#  @details This variable is set to Pin A0, the first pin on the Neucleo for motor 2.
#           This pin is set as an output. 
in1pin2=pyb.Pin (pyb.Pin.board.PA0, pyb.Pin.OUT_PP)
## @brief This variable is for the second pin of motor 2
#  @details This variable is set to Pin A1, the first pin on the Neucleo for motor 2.
#           This pin is set as an output. 
in2pin2=pyb.Pin (pyb.Pin.board.PA1, pyb.Pin.OUT_PP)
## @brief This variable is for the timer number associated with motor 2
timer2=5


#ENCODER PIN STUFF
## @brief This variable is for the frist encoder pin of encoder 1
#  @details This variable sets up the first pin of encoder 1 as Pin B6
ENCpin1=pyb.Pin (pyb.Pin.board.PB6)
## @brief This variable is for the second encoder pin of encoder 1
#  @details This variable sets up the second pin of encoder 1 as Pin B7
ENCpin2=pyb.Pin (pyb.Pin.board.PB7)
## @brief This variable is for the timer number associated with encoder 1
timernumber=4

## @brief This variable is for the frist encoder pin of encoder 2
#  @details This variable sets up the first pin of encoder 2 as Pin BC6
ENC2pin1=pyb.Pin (pyb.Pin.board.PC6)
## @brief This variable is for the second encoder pin of encoder 2
#  @details This variable sets up the second pin of encoder 2 as Pin BC7
ENC2pin2=pyb.Pin (pyb.Pin.board.PC7)
## @brief This variable is for the timer number associated with encoder 2
timernumber2=8


# SHARES
## @brief Shared Variable for duty of motor 1
#  @details This shared variable for the duty of motor 1 is set up to be 
#           a float. This is important because when we write to this variable in 
#           our closed loop controller, the number we calculate is a float. 
duty1 = task_share.Share ('f', thread_protect = False, name = "Duty_1")
## @brief Shared Variable for duty of motor 2
#  @details This shared variable for the duty of motor 2 is set up to be 
#           a float. This is important because when we write to this variable in 
#           our closed loop controller, the number we calculate is a float. 
duty2 = task_share.Share ('f', thread_protect = False, name = "Duty_2")
## @brief Shared Variable position of encoder 1
#  @details This shared variable for the position of motor 1 is set up to be 
#           a 16-bit unsigned int. This is important because when we write to 
#           this variable in our encoder driver, it is a 16 bit number (between
#           0 and 65535)
EncPosition = task_share.Share ('h', thread_protect = False, name = "Position_1")
## @brief Shared Variable position of encoder 2
#  @details This shared variable for the position of motor 2 is set up to be 
#           a 16-bit unsigned int. This is important because when we write to 
#           this variable in our encoder driver, it is a 16 bit number (between
#           0 and 65535)
EncPosition2 = task_share.Share ('h', thread_protect = False, name = "Position_2")
## @brief Shared variable for proportional gain of motor 1
#  @details This variable is set up as a float so that we can input decimal gains
#           to properly tune our system. This variable is shared between files but is 
#           set in the main file. 
Kp1 = task_share.Share ('f', thread_protect = False, name = "Proportional_Gain1")
## @brief Shared variable for proportional gain of motor 2
#  @details This variable is set up as a float so that we can input decimal gains
#           to properly tune our system. This variable is shared between files but is 
#           set in the main file. 
Kp2 = task_share.Share ('f', thread_protect = False, name = "Proportional_Gain2")
## @brief Shared variable for the setpoint of motor 1
#  @details This variable is set up as a float so that when we calculate the setpoint
#           from our Gcode, if it has a decimal result, the shared variable 
#           structure will allow for that value to be written to it. This variable 
#           is written in task1 and is read in our closed loop controller. 
setpoint1 = task_share.Share ('f', thread_protect = False, name = "Set_Point1")
## @brief Shared variable for the setpoint of motor 2
#  @details This variable is set up as a float so that when we calculate the setpoint
#           from our Gcode, if it has a decimal result, the shared variable 
#           structure will allow for that value to be written to it. This variable 
#           is written in task1 and is read in our closed loop controller. 
setpoint2 = task_share.Share ('f', thread_protect = False, name = "Set_Point2")

## @brief Shared variable for the z position for our half axis. 
#  @details This variable is either 0 or 1 depending on if we want our servo motor
#           to be down or up. This allows us to raise and lower our Sharpie for 
#           tracing the correct contours. 
zpos = task_share.Share ('h', thread_protect = False, name = "z_Position")
## @brief Shared variable to tell us when theta is ready to move
#  @details This variable is calculated in the closed loop controller
#           and tells us when theta position is within range of the setpoint.
#           This variable is important for our FSM. When it is set to 1, 
#           we calculate a new setpoint. When it is 0, we do not generate a new 
#           setpoint. This allows the motor to reach its setpoint before a new one 
#           is generated. 
THETAGO=task_share.Share ('h', thread_protect = False, name = "THETAGO")
## @brief Shared variable to tell us when R is ready to move
#  @details This variable is calculated in the closed loop controller
#           and tells us when R position is within range of the setpoint.
#           This variable is important for our FSM. When it is set to 1, 
#           we calculate a new setpoint. When it is 0, we do not generate a new 
#           setpoint. This allows the motor to reach its setpoint before a new one 
#           is generated
RGO= task_share.Share ('h', thread_protect = False, name = "RGO")
## @brief Shared variable for the value of our R limit switch
#  @details This variable contains the value of the pin that our limit switch is 
#           connected to. We are using this limit switch as a kill switch so that
#           when the pin value changes from 1 to 0, the duty to all our motors is 
#           set to 0. This prevents our motors from burning up when the parts reach 
#           a mechanical stop. 
Rswitch = task_share.Share ('h', thread_protect = False, name = "R_Switch")

setpoint1.put(0)     #Theta Setpoint (Degrees)
setpoint2.put(0)    #R setpoint (degrees) #Limit of 715
#Kp1.put(27)     #Theta Motor
Kp1.put(20)
#Kp2.put(7)      #R Motor
Kp2.put(10)

#OBJECTS
## @brief Variable for the Motor 1 object
motor1=MotorDriver.MotorDriver(en_pin, en_pin2, in1pin, in2pin, in1pin2, in2pin2, timer, timer2,duty1,duty2)
## @brief Variable for the Motor 2 object
motor2=MotorDriver.MotorDriver(en_pin, en_pin2, in1pin, in2pin, in1pin2, in2pin2, timer, timer2,duty1,duty2)
## @brief Variable for the Encoder 1 object
ENC1=EncoderDriver.EncoderDriver(ENCpin1,ENCpin2,ENC2pin1,ENC2pin2,timernumber,timernumber2,EncPosition,EncPosition2)
## @brief Variable for the Encoder 2 object
ENC2=REncoder.EncoderDriver(ENC2pin1,ENC2pin2,timernumber2,EncPosition2)

## @brief Variable for the Theta Control Loop object
ThetaControl=ThetaMotorControl.ThetaClosedLoop(Kp1,setpoint1,EncPosition,duty1,THETAGO)
## @brief Variable for the R Control Loop object
RControl=RMotorControl.RClosedLoop(Kp2,setpoint2,EncPosition2,duty2,RGO)

## @brief Variable for the pin our servo motor is connected to
#  @details This variable sets up our servo motor pin as pin A7
servopin = pyb.Pin (pyb.Pin.board.PA7, pyb.Pin.OUT_PP)
## @brief Variable for the timer for our servo motor pin (timer 17)
servotimer =17
## @brief Variable for the timer for our servo motor cahnnel (ch 1)
servoch = 1

## @brief Variable for the pin our first limit switch is connected to
#  @details This variable sets up our servo motor pin as pin A8 and uses a 
#           pull down resistor to ensure correct output.
switchpin1=pyb.Pin(pyb.Pin.board.PA8, pyb.Pin.IN, pyb.Pin.PULL_DOWN) #PB4
## @brief Variable for the pin our second limit switch is connected to
#  @details This variable sets up our servo motor pin as pin A6 and uses a 
#           pull down resistor to ensure correct output.
switchpin2=pyb.Pin(pyb.Pin.board.PA6, pyb.Pin.IN, pyb.Pin.PULL_DOWN)
## @brief Variable for the servo motor object
Servo=ServoMotorF.ServoMotorF(servopin, servotimer, servoch)
## @brief Variable for the limit switch object
LSwitch=ServoMotorF.LimitSwitch(switchpin1,switchpin2,duty2,Rswitch)

zpos.put(0)
#up is 0
#down is 1

THETAGO.put(1)
RGO.put(1)
def task1_fun ():
    '''!
        runs tasks and functions for the first motor
    '''
    
    print('Task1')
    with open('RTest.txt') as R, open('TTest.txt') as T: #draws rectangle
    #with open('RTest.txt') as R, open('TTest.txt') as T:    #draws CP Logo ish
        print('Opened Both Files Successfully')
        while True:
            #time.sleep(1)
            if THETAGO.get()==1:
                r=R.readline()
                print('r=',r)
                setpoint2.put(float(r)*2) #Mult by 2 for CP Divide for Rect
                THETAGO.put(0)
            elif THETAGO.get()==0:
                print('Not Moving R')  
                yield(0)
                
            if RGO.get()==1:
                #print('Theta Motor Working')
                t=T.readline()
                print('t=',t)
                setpoint1.put(float(t)*2)   #Mult by 2 for CP Divide for Rect
                RGO.put(0)
            elif THETAGO.get()==0:
                print('Not Moving Theta')
                yield(0)
            yield(0)
            
def task2_fun ():
    
         
        while True:
                print('Running Control Loop')
                
                ENC2.read()
                RControl.control_loop()
                motor2.set_duty_cycle2(duty2.get())
            
                ENC1.read()
                ThetaControl.control_loop1()
                motor1.set_duty_cycle(duty1.get())
                if LSwitch.checkswitch()==0:
                    motor2.set_duty_cycle2(0)
                    pass
                

                yield(0) 
def task3_fun():
    
    print('Task3')
    while True:  
        # LSwitch.checkswitch()
        LSwitch.checkswitch()  
        if zpos.get()==0:
            Servo.up()
            
        elif zpos.get()==1:
            Servo.down()  
        else: 
            pass
        yield (0)
        

if __name__=="__main__":
    while True:
        try:
            x = int(input())
            while True: 
                try: 
                    if x <= 10:
                        task1 = cotask.Task (task1_fun, name = 'Task_1', priority = 2, 
                                             period = 200, profile = True, trace = False)
                        task2 = cotask.Task (task2_fun, name = 'Task_2', priority = 3, 
                                             period = 10, profile = True, trace = False)
                        task3 = cotask.Task (task3_fun, name = 'Task_3', priority = 2, 
                                            period = 40, profile = True, trace = False)
                        
                        # task4 = cotask.Task (task3_fun, name = 'Task_4', priority = 3, 
                        #                      period = 20, profile = True, trace = False)
                        cotask.task_list.append (task1)
                        cotask.task_list.append (task2)
                        cotask.task_list.append (task3)
                        # cotask.task_list.append (task4)
                    
                        # Run the memory garbage collector to ensure memory is as defragmented as
                        # possible before the real-time scheduler is started
                        gc.collect ()
                    
                        # Run the scheduler with the chosen scheduling algorithm. Quit if any 
                        # character is received through the serial port
                        vcp = pyb.USB_VCP ()
                        while not vcp.any ():
                            cotask.task_list.pri_sched ()
                    
                        # Empty the comm port buffer of the character(s) just pressed
                        vcp.read ()
                        
                except KeyboardInterrupt:
                    break
        except :
            break
                

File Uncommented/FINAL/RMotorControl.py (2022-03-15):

"""
    @file                    RMotorControl.py
    @brief                   This file provides the code to run closed loop control on R motor
    @author                  Daniel Gonzalez
    @author                  Nolan Clapp
    @author                  Caleb Kephart
    @date                    March 8, 2022
"""
import utime
import time


class RClosedLoop:
    ''' @brief Puts system into a closed loop.
        @details This code allows us to run the motor/encoder system within a closed loop.
    '''
    
    def __init__(self,Kp2,setpoint2,EncPosition2,duty2,RGO):
        '''
            @brief          Constructs a closed loop object for R Motor
            @details        Sets up the closed loop so that it can intake data from the encoder and main to send to the motor driver.
            @param Kp2       This parameter allows us to choose the gain utilized by the system
            @param setpoint2    This parameter holds the desired motor position
            @param EncPosition2  This parameter allows for the class to intake the encoder position data
            @param duty2     This parameter chooses the duty cycle for the motor
            @param RGO   This parameter allows us to cycle through our FSM in main when we are within a desired range of our setpoint
        '''
        
        
        ## @brief System Gain for motor 1
        #
        self.Kp2=Kp2 
        ## @brief Desired encoder position
        #
        self.setpoint2=setpoint2
        ## @brief Actual Encoder Position
        #  @details Allows for the class to read encoder position data from the 
        #           encoder.
        #
        self.EncPosition2=EncPosition2
        ## @brief sets duty cycle for motor
        #
        self.duty2=duty2       
        ## @brief sets timer for data collection
        #
        self.RGO=RGO
        ## @brief array of time data
        #
        self.Time1=[]
        ## @brief array of actual position data
        #
        self.Pos1=[]
        ## @brief starting time of data collection 
        #
        self.starttime=time.ticks_ms()
        
            
    def control_loop(self):
        '''
            @brief Runs closed loop control on R motor
            @details This method runs the closed loop control system for the R motor. 
            we accomplish this by multiplying the difference between the setpoint and the 
            current position by a porportional gain. We then write this value to the duty
            that will be passed into our motor driver. 
        '''
        #Theta Direction
        #This calculates the correct setpoint based on shared x and y position values from GCode
        #R=math.sqrt(self.xpos.get()^2+self.ypos.get()^2)
        # Factor to convert from rotations (ticks) to linear position
        # 1 motor rotation= 1.51 inches in R direction
        #360 degrees = 4096*4 ticks (multiply desired degrees by 4096*4/360)
        #degtolin=4096*4/1.51
        #self.setpoint2.put(R*degtolin)
        
        ## @brief the error between actual and desired position
        self.error2=self.setpoint2.get()-self.EncPosition2.get()*360/(4096*4)
        if abs(self.error2)>=5:
            self.RGO.put(0)
            
        elif abs(self.error2)<5:
            self.RGO.put(1)
            
       
        ## @brief the duty cycle required for the system to correct with set gain.
      
        self.actuation2=self.Kp2.get()*self.error2
        
        self.duty2.put(self.actuation2)
       
    

















    # def printdata(self):
    #     '''!
    #         displays lists for time and encoder position while the task runs
    #     '''
    #     ## @brief index of arrays
    #     #
    #     n=0
    #     while n< len(self.Time1):
    #         print(self.Time1[n],',',self.Pos1[n])
    #         n=n+1
        

    
        
        
    
    
    
        

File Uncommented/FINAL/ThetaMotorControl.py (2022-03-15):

"""
    @file                    ThetaMotorControl.py
    @brief                   This file provides the code to run closed loop control on Theta motor
    @author                  Daniel Gonzalez
    @author                  Nolan Clapp
    @author                  Caleb Kephart
    @date                    March 8, 2022
"""
import utime
import time

class ThetaClosedLoop:
    ''' @brief Puts system into a closed loop.
        @details This code allows us to run the motor/encoder system within a closed loop.
        by calculating the actuation signal from the difference between the current 
        setpoint and current position multiplied by gain Kp1. 
    '''

    def __init__(self, Kp1, setpoint1, EncPosition1, duty1,THETAGO):
        ''' 
            @brief          Constructs a closed loop object for Theta Motor
            @details        Sets up the closed loop so that it can intake data from the encoder and main to send to the motor driver.
            @param Kp1       This parameter allows us to choose the gain utilized by the system
            @param setpoint1    This parameter holds the desired motor position
            @param EncPosition1  This parameter allows for the class to intake the encoder position data
            @param duty1     This parameter chooses the duty cycle for the motor
            @param THETAGO   This parameter allows us to cycle through our FSM in main when we are within a desired range of our setpoint

        '''
        # @brief System Gain for motor 1
        #
        self.Kp1 = Kp1

        # @brief Desired encoder position
        #
        self.setpoint1 = setpoint1

        # @brief Actual Encoder Position
        #  @details Allows for the class to read encoder position data from the
        #           encoder.
        #
        self.EncPosition1 = EncPosition1

        # @brief sets duty cycle for motor
        #
        self.duty1 = duty1

        # @brief sets timer for data collection
        #
        self.THETAGO=THETAGO
        # @brief array of time data
        #
        self.Time1 = []
        # @brief array of actual position data
        #
        self.Pos1 = []

        # @brief starting time of data collection
        #
        self.starttime = time.ticks_ms()


    def control_loop1(self):
        '''
            @brief Runs closed loop control on theta motor
            @details This method runs the closed loop control system for the theta motor. 
            we accomplish this by multiplying the difference between the setpoint and the 
            current position by a porportional gain. We then write this value to the duty
            that will be passed into our motor driver. 
        '''

        # Theta Direction
        # This calculates the correct setpoint based on shared x and y position values from GCode
        # 360 degrees = 4096*4 ticks (multiply desired degrees by 4096*4/360)
        # self.setpoint1.put(math.atan((self.ypos.get()/self.xpos.get())*180/math.pi)*16384/360)
        # print(self.setpoint1.get())
        # angle=self.setpoint1.get()*360/(4096*4)
        # print(angle)

        #r motor wont run unless theta go=true
        
        ## @brief the error between actual and desired position
        #  @detils Uses the encoder position in degrees and setpoint in degrees
        self.error1 = self.setpoint1.get()-self.EncPosition1.get()*360/(4096*4)
        if abs(self.error1)>=7 :
            print('OUTSIDE THETA RANGE')
            
            self.THETAGO.put(0)
        elif abs(self.error1)<7:
           # print('GETTING IN HERE')
            self.THETAGO.put(1)
        print('Theta Error:',self.error1)

        # @brief the duty cycle required for the system to correct with set gain.
        #
        self.actuation1 = self.Kp1.get()*self.error1

        self.duty1.put(self.actuation1)

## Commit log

2022-03-01 working servo and limit switches
2022-03-12 CAD Upload
    [2020.SLDPRT, 60TPulley.SLDPRT, 60TPulley.STL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]
2022-03-14 EncoderDriver Commented
2022-03-15 Servo Motor Documentation
